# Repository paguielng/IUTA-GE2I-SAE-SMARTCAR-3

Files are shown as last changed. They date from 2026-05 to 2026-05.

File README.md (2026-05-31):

# ST STM32: development platform for [PlatformIO](https://platformio.org)








PlatformIO IDE (https://platformio.org?utm_source=github&utm_medium=core)
    
1 Présentation du projet
   ---
1.1 Contexte
   ---
Une entreprise de jouet souhaite développer une voiture pilotée par smartphone, qui intègre plusieurs fonctionnalités comme l'anticollision, le signalement d'obstacle ……

1.2 Objectifs
---
Concevoir, vérifier et valider l'électronique et la programmation d'une voiture pilotée par smartphone afin de :
- Permettre le pilotage de la voiture à partir d'un joystick virtuel sur un smartphone
- Donner, à ce véhicule, de l’autonomie dans certaines prises de décision (anticollision)
- Fournir des informations visuelles et sonores au pilote

1.3 Description de l’existant
---
La voiture est une voiture Radio Commandée déjà existante au catalogue de l'entreprise. Toute l'électronique existante a été supprimée, tout le reste est conservé (carcasse, roues, moteurs, phares …). Les éléments suivants ont été ajoutés à l'intérieur :
- Un module pont en H de référence LF298 pour alimenter le moteur de direction et le moteur de propulsion dans les 2 sens de marche
- Un buzzer passif pour générer un signal avertisseur d'obstacle ou le klaxon
- Deux capteurs infrarouges Sharp de détection d'obstacle
- 6 accumulateurs AA NiMh de 1.2V et 2300mAh en série ou 1 pack batterie de 2 accumulateurs 18650 Li ion de 3.7V de 2600mAh.

1.4 Critères d’acceptabilité du projet
---
Le chef d'entreprise souhaite qu'à la fin de l'étude, lui soient fournis :
- Un dossier de fabrication de la carte électronique (cahier de fabrication + fichiers GERBER + fichier PROTEUS)
- Un dossier technique (cahier de laboratoire + documentation technique + simulations + schémas électriques, schéma d’implantation…)
- Une démonstration avec un prototype opérationnel
- Une étude de coût unitaire pour une production de 100 exemplaires
- Une étude d'autonomie voiture à l’arrêt

2 Expression des besoins
---
2.1 Besoins fonctionnel
---
- Un prototype
- Un dossier technique (cahier de laboratoire)
- Un dossier technique de fabrication (cahier de fabrication ……)
- Une démonstration du système opérationnel

2.2 Fonctionnement global attendu
---
- La voiture est pilotée par smartphone via liaison Bluetooth grâce à un joystick virtuel
- Des dispositifs de sécurité sont mis en œuvre sur la voiture tels que des capteurs de distance d’obstacle avant et arrière, et un avertisseur sonore en fonction de la proximité de l’obstacle.
- L'avertisseur sonore peut être activé directement comme klaxon grâce à un bouton poussoir virtuel sur le smart-phone. Il est aussi possible de générer une mélodie ou des fréquences fixes.
- Un bargraphe virtuel, sur le téléphone, permet d'informer visuellement l'utilisateur de la proximité de l'obstacle à l'avant et/ou du niveau de batterie. (Le niveau de batterie sera indiqué en permanence sauf si proximité d’obs-tacle à l’avant)
- Détection (Près, Moyen et Loin) respectivement moins de 40cm, entre 40 et 60cm et au-delà
- L’utilisateur peut choisir d’activer, de façon permanente, les phares avant et arrière de la voiture grâce à un switch virtuel sur l’écran du smartphone et au besoin de passer dans un mode de gestion automatique grâce à un capteur de luminosité.
- Les phares arrière s’allument plus fort en cas de freinage.
- La température extérieure est reportée sur le smartphone.

2.3 Fonctionnement détaillé attendu
---
- Deux détecteurs de distance infrarouge (un à l’arrière et l’autre à l’avant) permettent de mesurer la distance à l’obstacle et la vitesse d'approche du véhicule, et d’identifier la zone de proximité
- Un buzzer permet d’émettre des bips plus ou moins rapprochés en fonction de la distance à l’obstacle (2 bips par seconde dans la zone Moyen et 4 bips par seconde dans la zone près). Le klaxon est prioritaire sur les bips.
- Le véhicule réduit automatiquement de 50% la consigne de vitesse dans la zone moyenne lorsque le déplace-ment s’effectue vers l’obstacle.
- Le véhicule freine à fond (inversion de la propulsion à consigne maximale), jusqu’à arrêt du véhicule, lorsque le véhicule s’approche de l’obstacle dans la zone près, et cela quel que soit la consigne.
- Les phares arrière s’allument plus fort à chaque freinage.
- Les phares avant et arrière s’allument de façon permanente si le switch virtuel est dans la position “ON” et automatiquement en cas de faible luminosité si le switch est en position “AUTO”
- ,,,,,,,,,,,

3 Contraintes
---
3.1 Coûts
---
Aucune contrainte de coût n’est imposée. En revanche un calcul de coût unitaire pour une production de 100 cartes est attendu (composants électroniques + circuit imprimé + voiture + accessoires + main d'œuvre).

3.2 Autonomie de fonctionnement
---
La voiture doit avoir une autonomie d'au moins 30 minutes avec une batterie de 6 accumulateurs NiMh de capacité 2300mAh.

3.3 Délais de réalisation
---
2h C / 28h TD / 27h TP / 25h autonomie

4 Déroulement du projet
4.1 Séquencement
   ---
- Partie électronique du projet
- Partie Numérique du projet
- Dossier de conception (cahier de laboratoire + documentation technique + simulations)
- Dossier de fabrication (cahier de fabrication + fichiers GERBER + fichier PROTEUS)

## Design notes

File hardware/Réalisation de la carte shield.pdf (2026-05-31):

# Réalisation de la carte SHIELD smartcar

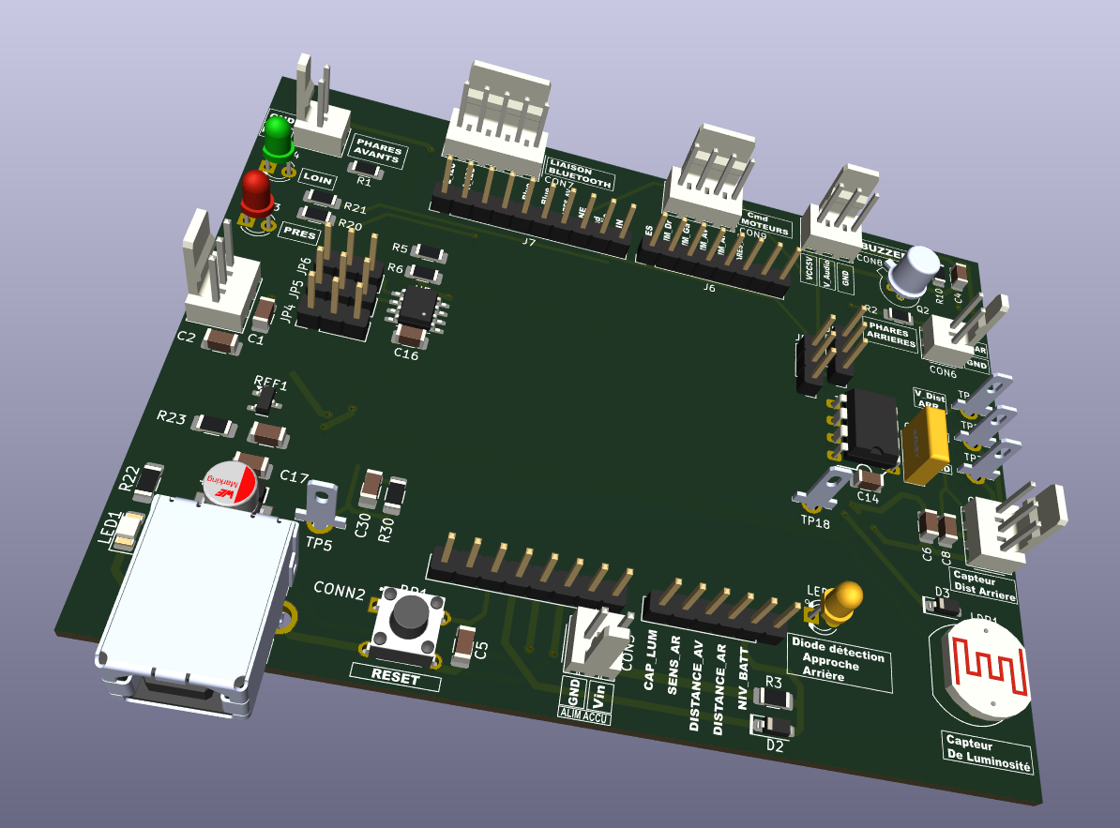
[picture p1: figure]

## I. Introduction

Le circuit imprimé est déjà commencé. Le projet KiCad se trouve dans le dossier Réalisation du circuit imprimé (https://toulouse3.sharepoint.com/:f:/r/sites/IUTA-BUTS2SAESMARTCAR_MDL/Documents%20partages/General/Partie%20Electronique/R%C3%A9alisation%20du%20circuit%20im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)

Vous devez au préalable regarder les vidéos suivantes : Alimentation en chaine (https://toulouse3.sharepoint.com/:f:/s/IUTA-BUTS2SAESMARTCAR_MDL/EhpyGaySZhJNksRkxSJ0DuYBxVbpqpTwTZGnaVfsGNpclQ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)

## II. Placement des composants

### 1) Listes des composants à placer, grille et pas de grille

- Zoom
La façon la plus simple de zoomer est d'utiliser la molette de la souris.
- La grille (voir page 27 du tutoriel)
La grille permet d'aligner tous les objets (composant, pistes, ..). Vous devrez toujours travailler en millième de pouce (mils) avec un pas de grille de 10millièmes de pouce 10 mils sauf lors de placement nécessitant une grande précision 2mils.
- Placer un composant (A partir de la page 29 du tutoriel)
- Rotation des composants ou sérigraphie grâce à la touche R après une sélection -
- Sélection d’une piste entière grâce à la touche U lors d’un survole de la souris
- Pour déplacer un composant déjà placer : clic droit pour le sélectionner puis maintient clic gauche pour le déplacer.

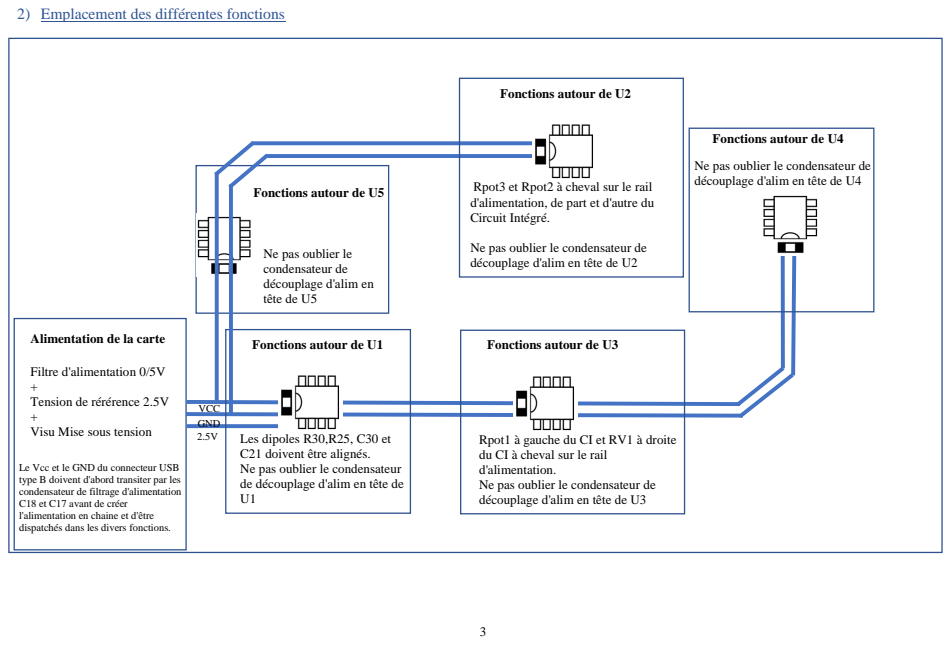
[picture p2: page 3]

2) Emplacement des différentes fonctions

Ne pas oublier le condensateur de
découplage d'alim en tête de U4

Rpot3 et Rpot2 à cheval sur le rail
d'alimentation, de part et d'autre du
Circuit Intégré.

Ne pas oublier le
condensateur de
découplage d'alim en
tête de U5

découplage d'alim en tête de U2

Les dipoles R30,R25, C30 et
C21 doivent être alignés.
Ne pas oublier le condensateur
de découplage d'alim en tête de

Rpot1 à gauche du CI et RV1 à droite
du CI à cheval sur le rail
d'alimentation.
découplage d'alim en tête de U3

Le Vcc et le GND du connecteur USB
type B doivent d'abord transiter par les
condensateur de filtrage d'alimentation
C18 et C17 avant de créer
l'alimentation en chaine et d'être
dispatchés dans les divers fonctions.

### 3) Placement de l'ensemble des composants

Avec la grille en système impérial, une grille de 10mils ou 2th.
- Placer U11 et les composants associés aux fonctions autour de ce Circuit Intégré (voir les directives de la page précédente).
- Placer U3 et les composants associés aux fonctions autour de ce Circuit Intégré (voir les directives de la page précédente).
- Placer U5 et les composants associés aux fonctions autour de ce Circuit Intégré (voir les directives de la page précédente).
- Placer U2 et les composants associés aux fonctions autour de ce Circuit Intégré (voir les directives de la page précédente).

## III. Routage

### 1) Les règles de conception

Les pistes possèdent des largeurs spécifiques suivants leur nature.
Les pistes d'alimentation repérées 5V et GND auront une taille automatique de 30mils et les vias associés seront des V70mils.
Les pistes de signal (toutes les autres pistes) auront une taille automatique de 20mils et les vias associés seront des V50mils.

Les règles d'isolement sont définies dans les options.
C’est-à-dire les distances minimums entre chaque entité.
- 10mils pour les distances minimum entre toutes les entités).
- Pad-Pad (distance minimale entre deux Pastilles) 10mils
- Pad-Trace (distance minimale entre une pastille et une piste) 10mils
- Trc-Trc (distance minimale entre deux pistes) 10mils
- Graphic (distance minimale entre deux graphiques) 10mils
- Edge (distance minimale avec le bord de la carte) 10mils

Rappel : 1mil est 1 millième de pouce
1 pouce est égal à 2.54cm soit 25.4mm
D'où 1mil = 0.0254mm

### 2) L'empilement des couches

Nous travaillerons sur une carte électronique double face, c’est-à-dire 2 couches de cuivre :
- Une couche de cuivre (de couleur rouge dans KiCad) sur le dessus de la carte ( Cette face se nomme côté composants car c'est sur cette face que nous trouvons, généralement, les composants électronique)
- Une couche de cuivre (de couleur bleu dans KiCad) sur le dessous de la carte (Cette face se nomme côté cuivre car c'est historiquement la face cuivrée des premiers Circuits Imprimés)

Nous utiliserons une épaisseur standard de cuivre de 35µm (Top copper et Bottom copper) sur une carte d'épaisseur finale 1,6mm. Le matériau central est de type FR4. Une couche de verni de 10µm (Top resist et

Les 2 couches de verni de 10µm | Les 2 couches de cuivre de 35 µm

La déclaration des couches se fait dans le menu « Options »

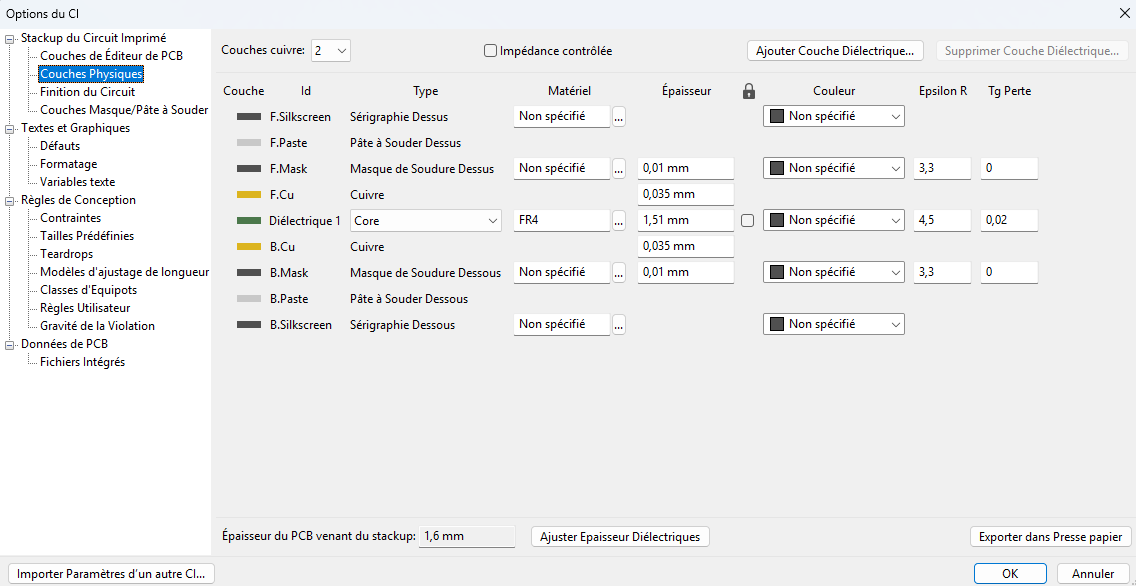
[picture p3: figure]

### 3) Les pistes

Remarques générales :
- Les pistes ne doivent pas faire de boucle sinon il risque d'y avoir du bruit électrique (parasites).
- Pas d’angle droit dans les changements de direction. Seuls les changements de direction à 45° sont autorisés.
- Pas d’angle inférieur à 90° dans les raccords de piste
- Routage automatique interdit car ne respecte pas les règles de placement et de réduction du bruit.
- Visionner les vidéos sur le routage
a) Pistes d'alimentation en chaine

Les pistes d'alimentation 5V et GND autorisant l'alimentation en 0/5V de toutes les fonctions doivent, à partir des condensateurs de filtrage d'alimentation C18 et C17, cheminer parallèlement avec un écart de 10th (2 carreaux avec une grille de 5th) sur le côté cuivre.
Les pistes d'alimentation sont déjà tirées, il manque juste à les raccorder à la sortie du filtre d'alimentation composé de C18 et C17.
Ce cheminement parallèle des pistes d'alimentation permet de limiter les parasites électromagnétiques engendrés par les fluctuations de courants sur les liens d'alimentation.

La tension de référence 2,5V fournit par REF1 doit transiter par le condensateur de découplage C19 avant d’être raccordée à U1

Voir page 3 pour la vue d'ensemble et les directives supplémentaires.

En vous aidant du tutoriel KiCad tracer les 3 arrivées GND, VCC et 2,5V et raccordez les au rail d'alimentation déjà tiré.

L'alimentation des différentes fonctions se fait en repiquant les 2 liens d'alimentation en un seul endroit du cheminement de l'alimentation en chaine.

Router l'ensemble des composants de la fonction "Alimentation".

b) Condensateur de découplage d'alimentation
Les condensateurs de découplage d'alimentation sont présents pour filtrer les fluctuations de tension sur les pistes d'alimentation.
Les pistes d'alimentation, des fonctions concernées par ces condensateurs, doivent tout d'abord transiter par ces condensateurs avant d'alimenter la fonction.

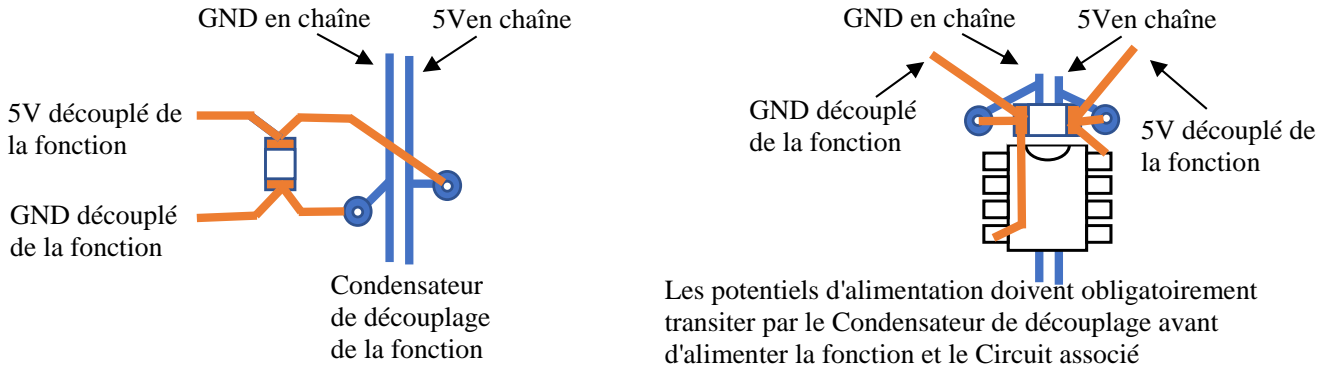
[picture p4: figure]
Condensateur de découplage de la fonction; 5V découplé de la fonction; GND découplé de la fonction; GND en chaîne; 5Ven chaîne; GND découplé; de la fonction; 5V découplé de; la fonction; Les potentiels d'alimentation doivent obligatoirement

c) Les composants d'une fonctions
Tous les composants de chaque fonction se situent dans la même zone de la carte de façon à minimiser les longueurs des pistes. Si ce n'est pas le cas retoucher votre placement.

Router l'ensemble des composants fonction par fonction.

d) Alimentation locale des fonctions
L'alimentation de chaque fonction devra s'effectuer exclusivement via le condensateur de découplage si celui-ci existe.
Alimentation locale d'une fonction => L'alimentation de chaque fonction ne peut se faire qu'en un seul point ou zone sur l'alimentation en chaine. Interdiction de se repiquer à plusieurs endroits (ne pas suivre le chevelu

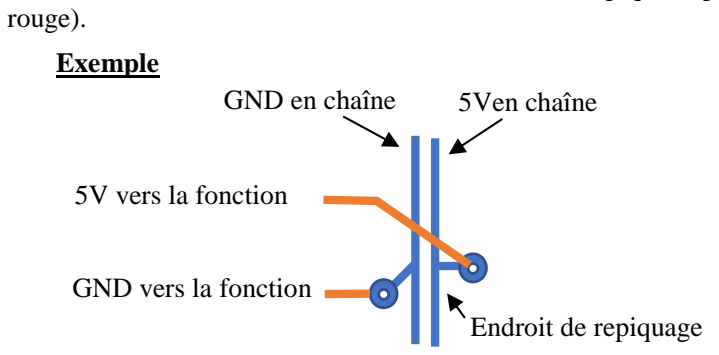
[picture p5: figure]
rouge).; GND en chaîne; 5Ven chaîne; GND vers la fonction; 5V vers la fonction; Endroit de repiquage; Exemple

e) Vérification d'absence d'erreur DRC
Vous devez avoir ces informations en bas à droite de la fenêtre : | et
Si non, vous devez corriger les erreurs.
Les erreurs DRC sont les erreurs où vous ne respectez les distances d'isolements et les erreurs CRC sont des oublis de pistes.

## IV. Sérigraphie

La sérigraphie constitue l'ensemble des écritures, indications et dessins qui seront sérigraphiés sur le verni de la carte.
Nous écrirons uniquement sur le côté composant. Ce qui correspond à la couche | mais nous
aurions pu écrire sous la carte (coté cuivre) ce qui correspond à la couche | . Sur le côté
cuivre les écritures et dessins apparaissent Rose et les écritures sont en mirroir.

transiter par le Condensateur de découplage avant d'alimenter la fonction et le Circuit associé

### 1) Le nom des composants

Tous les composants sont repérés par un nom. Par exemple :
- les résistances sont repérées par le suffixe R suivi d'un nombre
- les condensateurs sont repérés par le suffixe C suivi d'un nombre
- …

Cela permet non seulement de repérer l'emplacement physique des composants au moment du placement mais aussi de repérer les points de mesures pour des tests ou dépannages futurs.

La sérigraphie ne peut se faire sur les zones exemptent de vernis comme les pastilles. En effet les pastilles des empreintes des composants ne sont pas recouvertes de vernis de façon à permettre la soudure.

En vous plaçant sur une petite grille, 5th par exemple, affiner la position du nom des composants de façon à pouvoir lire les écritures même si les composants sont en place.

Pour modifier l'angle d'écriture sans modifier la position de l'ensemble du composant :
Clic droit sur le nom du composant pour le sélectionner puis clic gauche pour le sélectionner + R

Quelques exigences :
- Le nom du composant doit pouvoir être lu après la soudure de celui-ci => Pas de nom sous le composant.
- Les noms des composants proches devront, si possible, être alignés verticalement ou horizontalement
- Les noms des composants peuvent être au besoin tournés de 90° dans le sens trigonométrique
- L'ensemble des écritures et dessins doit apparaitre en jaune pâle
- Aucun dessins ou écritures ne doit apparaitre en rose (écriture en dessous)

### 2) Noms du binôme et personnalisation

Placer vos noms et groupe sur la carte avec une police de caractères "Arial Black" et une hauteur de 0,1inch.

Customiser votre carte en ajoutant une image ou photo monochrome.

## V. Création des fichiers de fabrication

Utiliser le tutoriel KiCad

Le fichier gerber ZIP est l'élément essentiel du dossier de fabrication.

## VI. Règles de notation appliquées colonne D du fichier de validation

- L'alimentation doit être en chaine ne doit pas comporter de boucle (-0.5 si non respecté)
- Les condensateurs de découplage doivent être très proche du circuit intégré (s'il y en a un) et respecter les règles de routage (voir III.3)b)) (1 point si correcte, 0.5 point si 1 erreur, 0 point sinon)
- Les composants doivent être regroupés par fonction (1 point si correcte, 0.5 point si 1 erreur, 0 point sinon)
- Les GND et VCC de chaque fonction doivent être pris localement sur le condensateur de découplage d'alimentation (1 point si correcte, 0.5 point si 1 erreur, 0 point sinon)
- Les noms du binôme et le groupe doivent être présent (0.5 point)
- Les noms des composants sont lisibles après soudure des composants (0.5 point)
- Les pistes autorisées sont horizontal, vertical et à ±45° (si non -0.5point)
- S'il existe des pistes manquantes (-1 point)

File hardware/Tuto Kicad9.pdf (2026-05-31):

1 | CDS

Christophe DOS SANTOS

# KiCad 9

## Table des matières

e) Transfert d’un ou plusieurs composant(s) d’une librairie à une autre ( méthode 2) 18 c) Placer précisément un composant avec l’outil de positionnement interactif ....31

## I. Saisie de schéma

1) Généralités
2) Importer un schéma électrique non KiCad

Numérotation automatique dans l’ordre de dépôt

Fils uniquement horizontaux et verticaux

Grille nécessaire pour un alignement des composants.

Possibilité de numérotation automatique des composants, à postériori.

3) Feuille de travail et cartouche
4) Dépôt du symbole d’un composants, en librairie, sur le schéma
Click | Indiquer le nom du composant à placer
| Sélectionner la version du composant

Sélectionner
l’empreinte du
composant

Cliquer ici si dépôt de
plusieurs instances

Click

Taille de la
feuille

Renseignements

5) Propriétés des composants
Pour éditer les propriétés d’un composant
6) Grille
Changement de grille par clic droit sur la feuille

La gestion de la grille par type d’objet se fait à partir du menu « préférences » puis « Préférences »

Click droit

Référence du composant
Valeur du composant

Ajouter une
propriété
comme la
référence
vendeur

7) Arrivées des potentiels d’alimentation (POWER)
Sous kicad il est nécessaire d’ajouter un POWER FLAG pour identifier les sources d’alimentation. Sans POWER FLAG vous obtiendrez des warnings au moment de la vérification des règles électriques.
8) Contrôle des règles électriques

Exemple de POWER FLAG

Le POWER FLAG
est accessible
dans la librairie
« Power »

9) Assigner les empreintes aux composants du schéma

Remarque : Certaines empreintes notamment celles des résistances CMS sont légèrement plus grande pour la soudure à la main. Elles sont annotées « Hand_Solder »

Click

Filtrer par librairie

1) Sélectionner le composant
2) Sélectionner la librairie
4) Sélectionner l’empreinte
3) Afficher l’empreinte
5)Afficher la vue 3D de l’empreinte | 6) Sauvegarder les modifications

Click droit sur un
composant de la liste
pour faire apparaitre un
menu contextuel

Copier l’empreinte du
composant sélectionné

Coller l’empreinte
précédemment copiée

## II. Symboles électriques et librairies

1) Créer un symbole
a) Lancer l’éditeur de symbole
b) Créer un symbole à partir d’un composant existant

Clic sur l’éditeur de symbole pour lancer la fenêtre dédiée

Chercher un
composant qui
se rapproche le
plus du
composant à
dessiner

Ajouter des entrées ou des sorties. Modifier le corps du symbole, les noms des E/S, les numéros de broche, le texte ….

Dans le menu fichier | Donner un nom au composant

Sélectionner une librairie personnelle si elle existe

Créer une nouvelle librairie si vous ne possédez pas de librairie personnelle ou souhaitez créer une autre librairie.

c) Créer un symbole de A à Z

Clic sur l’éditeur de symbole pour lancer la fenêtre dédiée

Choisir la librairie de
destination puis
cliquer sur nouveau
composant

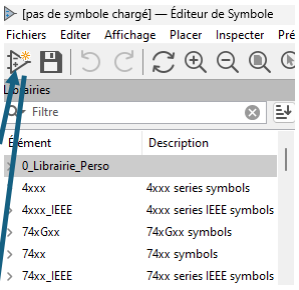
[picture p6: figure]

Nom du nouveau composant

Si le composant existe déjà dans une autre librairie

Préfixe du composant (exemple R pour resistor)

Nombre de composants identiques dans le même boitier

Clic gauche sur le corps pour accéder aux propriétés

Dessiner le composant

Choisir » remplir avec » pour donner une couleur au fond

Dessiner le corps du composant avec des formes prédéfinies, des arcs, des segments …..

Clic gauche pour commencer, clic gauche pour les changements de direction puis double clic gauche pour finir.

Dessiner le composant (suite)

Dessiner les broches
Placer du texte
Placer du texte dans une
boite

Accéder aux propriétés du symbole

Visibilité et apparence du nom et de la valeur
Localisation de l’empreinte dans les librairies d’empreinte.
URL de la documentation

Description du composant : Fonction, empreinte, ….

Choisir la couleur du corps désirée, ici jaune pâle.

Placer des mots clés comme par exemple : résistance, AOP, régulateur…

Donner un nom

2) Listes des sites permettant de télécharger des symboles
- Outils du revendeur Mouser : https://www.mouser.fr/electronic-cad-symbols-models/
- SnapEda : https://www.snapeda.com/
- SamacSys : https://www.samacsys.com/
- Les sites de revendeur comme Farnell et Radiospares

Sauvegarder le
composant

Clic

référence revendeur, le prix, ….

3) Les librairies de symboles
a) Emplacement des librairies et généralités Les librairies de base de Kicad se situent par défaut :

Les librairies personnelles ou propre au projet se situent par defaut :

Ne pas utiliser ou créer des librairies dans « Documents » si vous souhaitez une portabilité du projet.

(Voir f) Portabilité des librairies)

Pour configurer les librairies :

Examinateur de librairies de composants.
Permet de visionner les symboles des librairies mais pas de configurer les librairies.

Click

Ensemble des
librairies globales

de composants
disponibles

Possibilités d’ajouter
ou de supprimer des
librairies

Librairies utilisées pour la portabilité du projet

(Voir f) Portabilité des
librairies)

b) Création d’une librairie par importation d’un symbole de composant
Après téléchargement des fichiers, le fichier correspondant au symbole se termine avec l’extension .kicad_sym ou .lib.

Clic

1)Clic pour
ajouter la
librairie qui
contient le
nouveau
symbole

2)Une nouvelle ligne
apparaît | 4)Clic sur le dossier pour
| rechercher le fichier librairie
| de symboles

5)Sélectionner le fichier désiré

Clic

3)Donner un nom évocateur à cette librairie

Le fichier est en .sym pour symbol

Librairies utilisées pour la portabilité du projet
(Voir f) Portabilité des
librairies)

c) Ajout d’un composant dans une librairie existante
d) Transfert d’un composant d’une librairie à une autre (méthode 1)

1)Clic sur éditeur de symbole

Dans le fichier schématique

Ou

Dans le fichier projet

2)Clic droit sur la
librairie de
destination

3)Choisir le
symbole à
importer

2)Sélectionner
une librairie

1)Clic sur éditeur de symbole

Dans le fichier schématique

Ou

Dans le fichier projet

Sélectionner la librairie de destination -> clic droit -> coller

e) Transfert d’un ou plusieurs composant(s) d’une librairie à une autre ( méthode 2) Ouvrir le fichier de la librairie, où se situe le composant, avec un éditeur de texte.

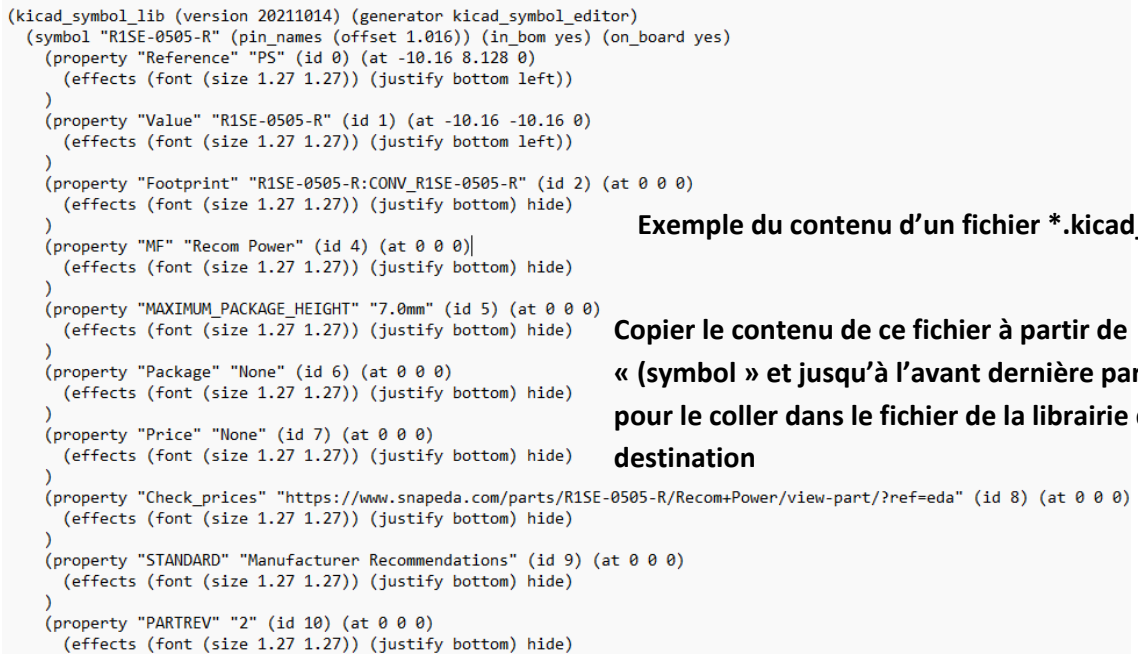
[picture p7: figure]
destination

Ouvrir le fichier de la librairie de destination dans l’éditeur de texte et se placer juste avant la dernière parenthèse et coller le contenu du fichier précédent.

Puis enregistrer ce fichier

Exemple du contenu d’un fichier *.kicad_sym

Copier le contenu de ce fichier à partir de
« (symbol » et jusqu’à l’avant dernière parenthèse pour le coller dans le fichier de la librairie de

3)Sélectionner le ou les
composants à transférer
puis clic droit

Copier ou Couper suivant
que vous souhaitez laisser une copie.

Remarque : L’ancienne librairie peut être supprimée.

f) Portabilité des librairies Voir : page 64
4) Liste du matériel BOM (Bill Of Material)

Sélectionner la librairie
à supprimer puis poubelle

Dans le menu « outils »

Sélectionner les champs
intéressant. Ici référence, valeur, quantité et
regroupement par valeur

Choisir le
format de
sortie CSV
pour l’ouvrir
avec excel ou
autre

Création
du fichier

## III. Création du PCB

1) Contrôle des règles électriques du schéma
2) Lancer l’éditeur de PCB

Clic sur l’éditeur de PCB pour lancer la fenêtre dédiée

L’ensemble des
composants à placer est
regroupé au milieu.

ClickC

Click

Toutes les erreurs ou avertissements signalés ici sont indiquées sur le PCB par une flèche de couleur.

Clic droit sur l’erreur ou l’avertissement pour être placé à l’endroit exact du PCB.

Nécessaire pour détecter d’éventuelles erreurs électriques

Toutes les règles de
violation sont
accessibles ici

3) Définition des Propriétés du projet
a) Les couches graphiques

Dans le menu « fichier » choisir Options « CI »

OU

Directement par l’icone

Pochoir pour le dépôt de pâte à braser sur le dessus Sérigraphie sur le dessus
Emplacement du vernis sur la couche du dessus Emplacement du Cuivre sur la couche du dessus

Sérigraphie sur le dessous

Bord de la carte

Emplacement du Cuivre sur la couche du dessous Emplacement du vernis sur la couche du dessous

Pochoir pour le dépôt de pâte à braser sur le dessous

b) Les couches physiques (Données fournies sur le site du fabricant)
c) Finition du cuivre (Voir possibilités du fabriquant)
d) Définitions des frontières Vernis/Masque/cuivre

e) Propriétés du texte et graphiques en fonction des couches
f) Contraintes d’isolement/de perçage g) Classes d’équipotentielles
Afin de gérer automatiquement les largeurs de pistes il est intéressant d’assigner des largeurs de piste aux équipotentielles de la carte.
Nous allons définir 3 classes :
- VBATT : Alimentation commune de la carte et des moteurs à partir des batteries ; largeur de piste 30th soit 0.762mm et via de 70th soit 1.78mm
- POWER : Alimentation 5V et GND de la partie commande de la carte ; largeur de piste de 20th soit 0.508mm et via de 50th soit 1.27mm
- DEFAULT : Tous les autres potentiels ; largeur de piste de 15th soit 0.38mm et via de

Une fois défini les classes d’équipotentielles il faut les assigner sur la schématique.

Remarques :

- Faire de même pour tous les fils en lien avec les équipotentielles autres que défaut.
- Ne pas oublier de mettre à jour le PCB à partir du schéma.
h) Taille des pistes et vias prédéfinie

70 mils35 mils70 mils

Clic droit sur le fil pour faire apparaitre le menu contextuel du fil.

Clic

Choisir la classe
d’équipotentielle,
précédemment crée,
correspondant aux pistes
d’alimentation 5V. (ici
« power »)

Clic

Clic
OU

Clic

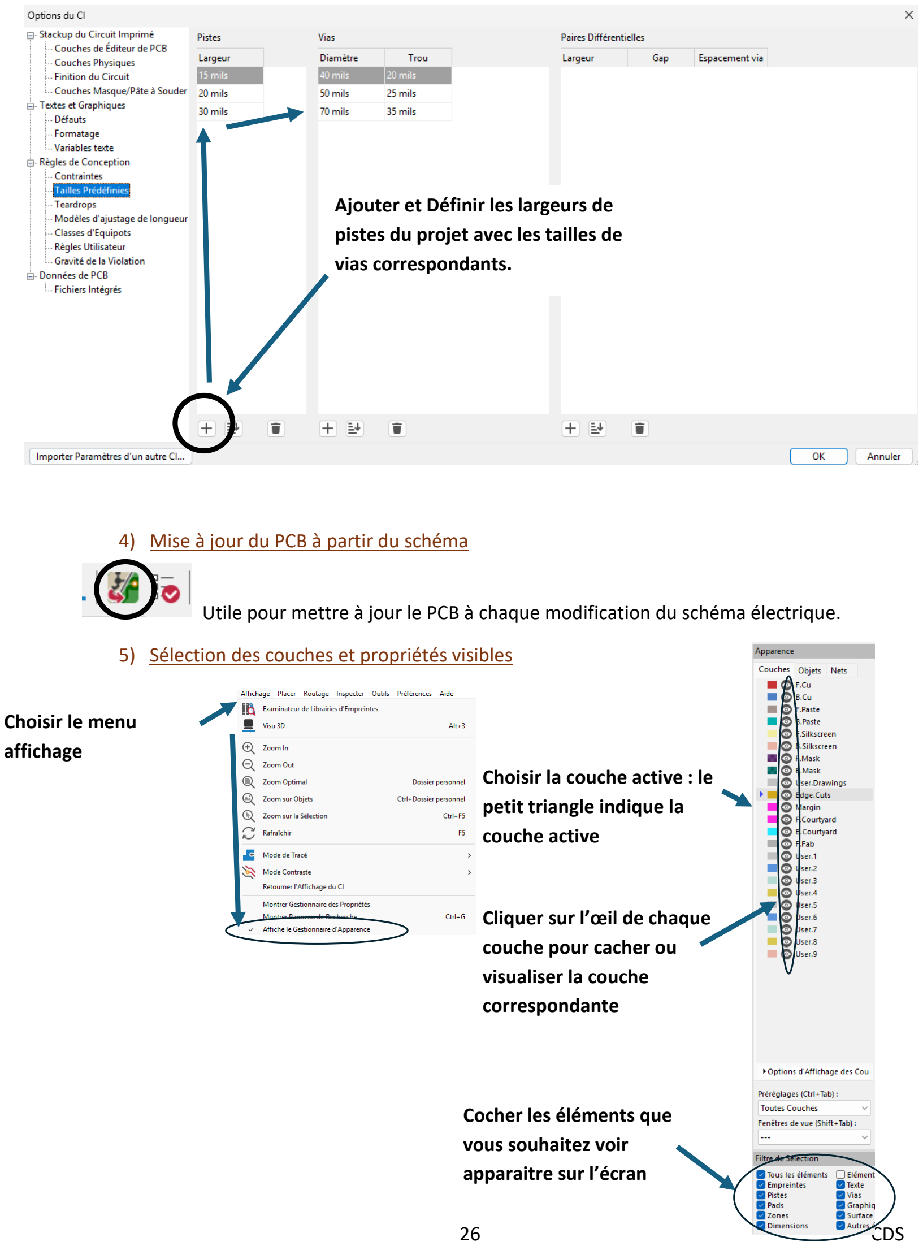
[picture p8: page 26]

4) Mise à jour du PCB à partir du schéma

Utile pour mettre à jour le PCB à chaque modification du schéma électrique.

5) Sélection des couches et propriétés visibles

Choisir le menu
affichage
Choisir la couche active : le petit triangle indique la
couche active

Cliquer sur l’œil de chaque couche pour cacher ou
visualiser la couche
correspondante

Cocher les éléments que
vous souhaitez voir
apparaitre sur l’écran

Ajouter et Définir les largeurs de pistes du projet avec les tailles de vias correspondants.

6) Choix du pas de grille et de la couche de travail
7) Tracer des contours et des trous de fixation de la carte
a) Choisir la couleur des bords de la carte
Choix du pas de grille | Choix de la couche de
| travail

Afficher la grille
Activer la grille
Choisir l’unité d’affichage des longueurs

b) Choix de la couche et de la grille

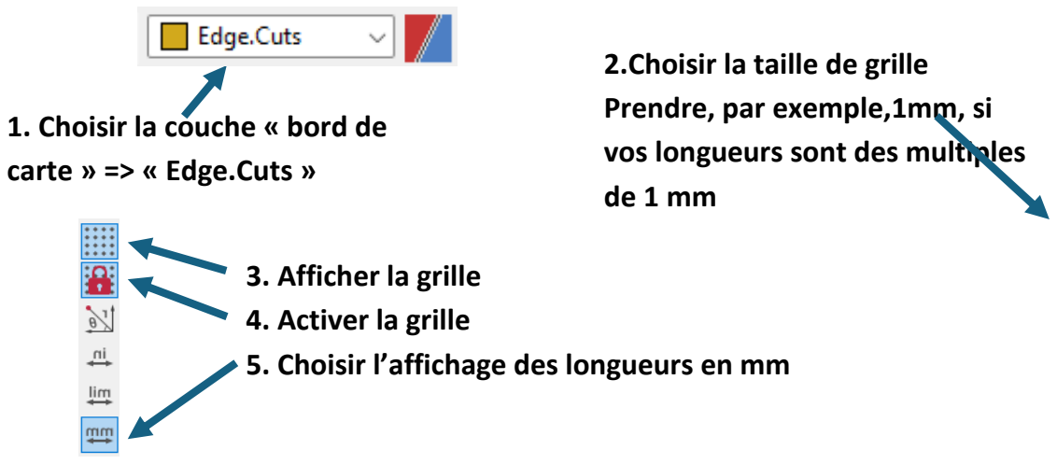
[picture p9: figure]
1. Choisir la couche « bord de carte » => « Edge.Cuts »; 2.Choisir la taille de grille Prendre, par exemple,1mm, si vos longueurs sont des multiples de 1 mm; 3. Afficher la grille 4. Activer la grille

c) Tracer du contour de la carte
d) Tracer les trous de fixation

### 5. Choisir l’affichage des longueurs en mm

Un clic gauche pour initier le tracé et un deuxième clic gauche pour finir le tracé

Les dimensions de la forme sont indiquées au cours du tracé

Choisir la couche « bord de carte » => « Edge.Cuts »

1.Choisir l’outil
Tracer Cercles

2.Clic gauche au centre du cercle puis deuxième clic
gauche lorsque le rayon
désiré est atteint.

8) Placement des composants
a) Tracer des cotes pour l’aide au placement
Se placer avec un affichage des longueurs en mm

A l’aide de l’outil de cotation tracer toutes les cotes.

Un gauche clic pour débuter la cote et un deuxième clic gauche
pour terminer la cote, puis un troisième clic gauche pour la positionner

Remarque : Pour cette phase il est bien de rester sur une grille en mm.

b) Placer les composants
Tous les composants à placer sont regroupés sur une partie de l’écran :

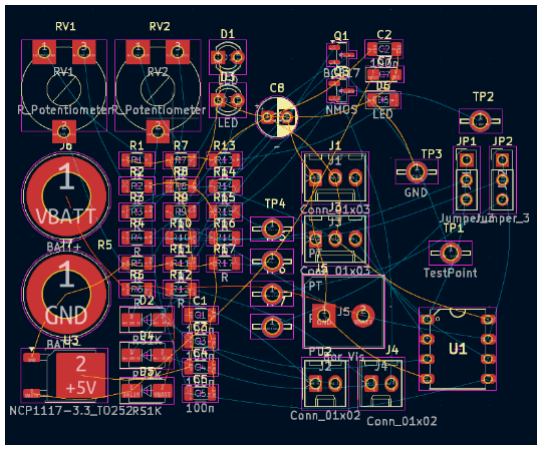
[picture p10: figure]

- Si certains composants à placer sont positionnés au mm alors se placer sur une grille en mm
sinon se placer sur une grille en th ou mils (25mils) car la plupart des empreintes ont été crées sur des grilles en mils ou th. Ceci permettra un bon alignement des pistes entre les composants.
- Choisir l’outil de sélection
- Clic gauche sur la sérigraphie du composant à placer pour le mettre en surbrillance puis maintien clic gauche pour le déplacer (ou touche M).

Raccourci

« M »

- Clic droit sur le composant pour ouvrir le menu contextuel afin de le manipuler et de

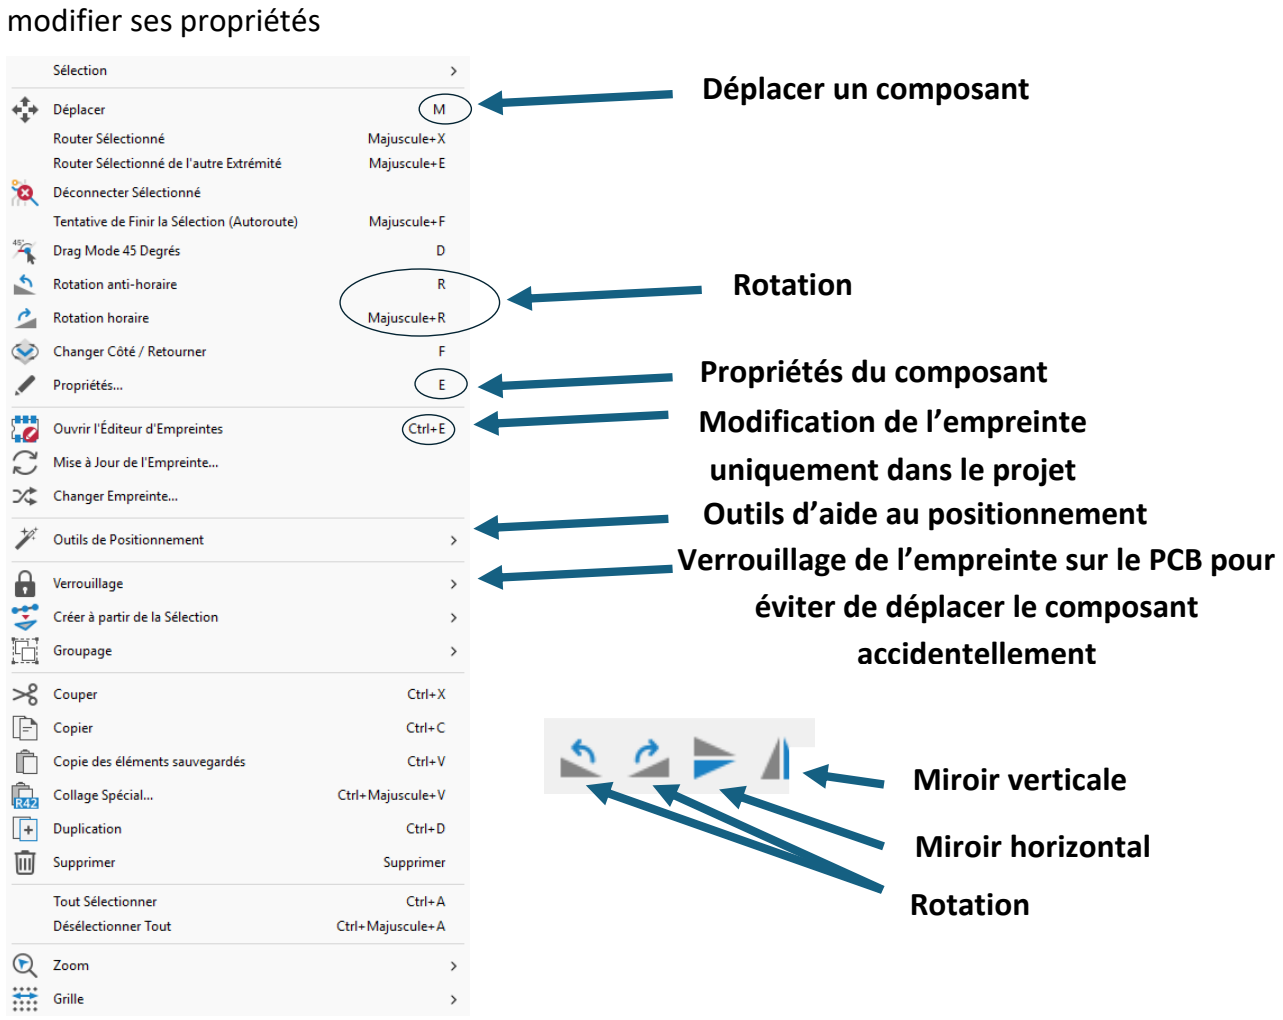
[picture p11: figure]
modifier ses propriétés; Déplacer un composant; Rotation; Propriétés du composant; Modification de l’empreinte uniquement dans le projet; éviter de déplacer le composant accidentellement; Outils d’aide au positionnement; Miroir verticale; Miroir horizontal

Verrouillage de l’empreinte sur le PCB pour c) Placer précisément un composant avec l’outil de positionnement interactif 1.Clic droit sur le
composant à placer pour
le sélectionner

2.Clic

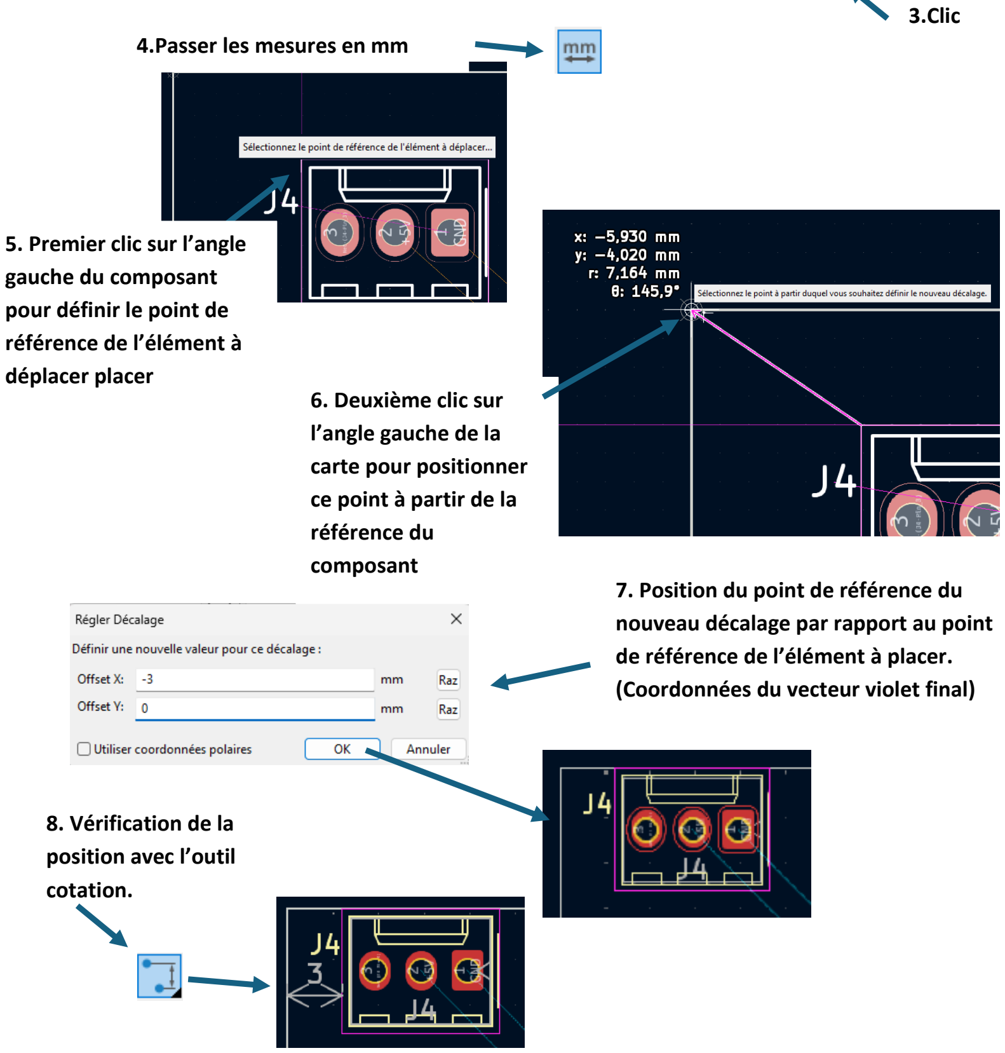
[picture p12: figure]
3.Clic; 4.Passer les mesures en mm; 5. Premier clic sur l’angle gauche du composant pour définir le point de référence de l’élément à déplacer placer; 6. Deuxième clic sur l’angle gauche de la carte pour positionner ce point à partir de la référence du composant; 7. Position du point de référence du nouveau décalage par rapport au point de référence de l’élément à placer. (Coordonnées du vecteur violet final); 8. Vérification de la position avec l’outil cotation.

d) Déplacer un composant avec les pistes
9) Tracer une piste
a) Taille de la piste
b) Couche de la piste
c) Pas de la grille

Choisir l’outil
Tracer de piste

Choisir une taille de
piste prédéfinie

Choisir une taille de piste automatique (voir Classes
d’équipotentielles)

Choisir la couche
concernée

Choisir le pas de la
grille

OU Touche « + » ou « - «

4.Touche « B » pour prendre en compte les

d) Tracé de la piste
e) Changement de couche par la création d’un via
10) Modification d’une piste
a) Sélectionner la piste
- Clic gauche sur la piste pour sélectionner un segment
- Survoler la piste + U : permet de sélectionner une piste entre 2 pastille ou embranchement.
- CTRL + clic gauche pour sélectionner plusieurs segments
b) Changer la taille d’une piste
Clic droit sur la piste sélectionnée pour faire apparaitre le menu contextuel.

Clic gauche sur la
pastille de départ

Clic gauche sur la
pastille de d’arrivée

Clic gauche à chaque changement de direction si nécessaire

Clic sur propriétés

Changer la taille de la piste.
Se placer au préalable en mm ou en mils pour obtenir les mesures dans l’unité souhaitée.

Clic droit sur la piste à l’endroit du via
OU
Touche de raccourci : V + clic gauche

c) Suppression des pistes
Suppression des pistes sélectionnées : touche « Suppr »
11) Tracer la sérigraphie d’une empreinte

Exemple de tracé

Choisir l’outil de tracé

La couche
sérigraphie du
dessus doit être

Tracé d’un trait de 4.95mm de hauteur

Choisir l’outil de duplication pour dupliquer la ligne de 5mm (préférer le raccourci « Ctrl + D »

Choisir l’outil de rotation pour tourner de 90° la ligne dupliquée (préférer le raccourci « R »)

Nous n’avons pas tracé un carré pour pouvoir opérer la modification ci dessous

Se placer dans l’éditeur d’empreinte

12) Modifier les propriétés de la pastille par défaut

Raccourcir les 2 côtés de l’angle en haut à gauche.

Ajouter un segment pour indiquer le sens du composant borne

Ajouter un cercle pour indiquer la borne 1 du composant

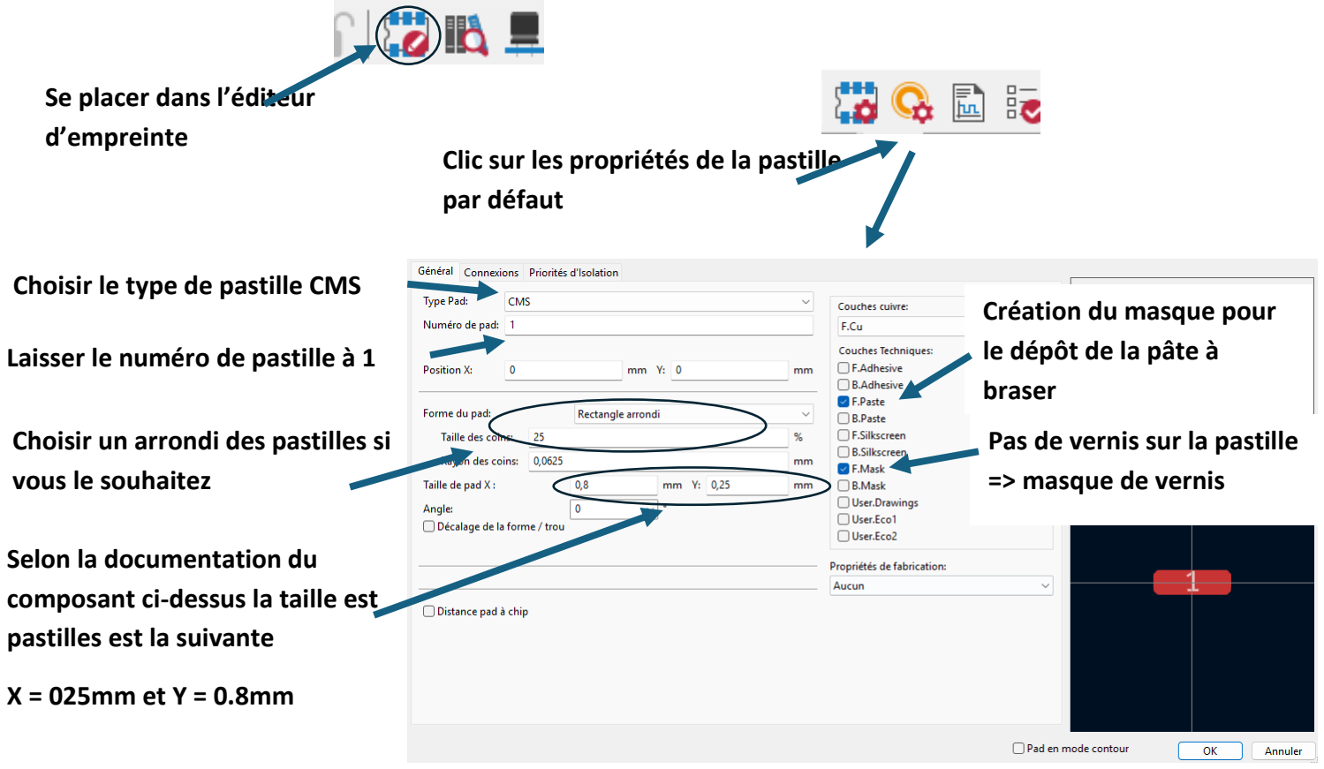
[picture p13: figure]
Clic sur les propriétés de la pastille par défaut; Choisir le type de pastille CMS; Choisir un arrondi des pastilles si vous le souhaitez; Selon la documentation du composant ci-dessus la taille est pastilles est la suivante; Laisser le numéro de pastille à 1; Pas de vernis sur la pastille => masque de vernis; Création du masque pour le dépôt de la pâte à braser; Se placer dans l’éditeur d’empreinte

13) Modification des propriétés d’une pastille

Clic droit sur la pastille pour afficher et modifier les propriétés (voir ci-dessus)

14) Dupliquer et modifier l’orientation des pastilles Exemple de création

Se placer dans l’éditeur
d’empreinte

Les pastilles commencent à 0.6 du bord et sont espacées de 0.5mm

Choisir l’outil de mesure pour repérer cette distance de 0.6mm

Avec l’outil de sélection ,la duplication « Ctrl+D », la rotation « D », la désélection « Ctrl + clic gauche » placer les 24 autres pastilles

Se placer dans l’éditeur
d’empreinte

15) Numéroter les pastilles

Un clic gauche sur chaque pastille dans l’ordre de numérotation.

16) Création de la zone d’exclusion de l’empreinte
Cette zone permet de définir l’occupation physique du composant et de prévenir tout chevauchement avec des composants voisins

Choisir la couche de travail pour délimiter la zone d’occupation de l’empreinte

Choisir une grille avec un pas de 0.05mm ce qui correspond à environ 2 millièmes de pouce

Choisir l’outil de dessin trait et tracer 4 traits à 0.25mm de l’empreinte soit environ 10 millièmes de pouce.

Clic droit sur la zone de travail pour accéder au menu contextuel

17) Création de pad thermique pour la diffusion de la chaleur Exemple de création de pad thermique

Résultat avec 25 pads thermiques

Clic

Clic droit sur la pastille pour accéder au menu contextuel et la modifier en rectangle
3.7mm*3.7mm

Numéroter la pastille 33

Choisir Pad traversant

Numéro 33

Aucune couche
technique

Choisir Pad
thermique

Diamètre de la
pastille 0.5mm

Diamètre du trou
0.2mm

18) Création des emplacements de dépôt de pâte à braser
Exemple
Définition des emplacements de dépôt de la pâte à braser qui évitent les trous des vias thermiques.
Se placer sur la couche
de la pâte à braser du
dessus

Utiliser l’outil de tracé de polygone pour tracer la zone de base qui sera dupliquée.

Dupliquer et étendre cette zone sur l’ensemble de la
pastille.

19) Vérifier la validité d’une empreinte

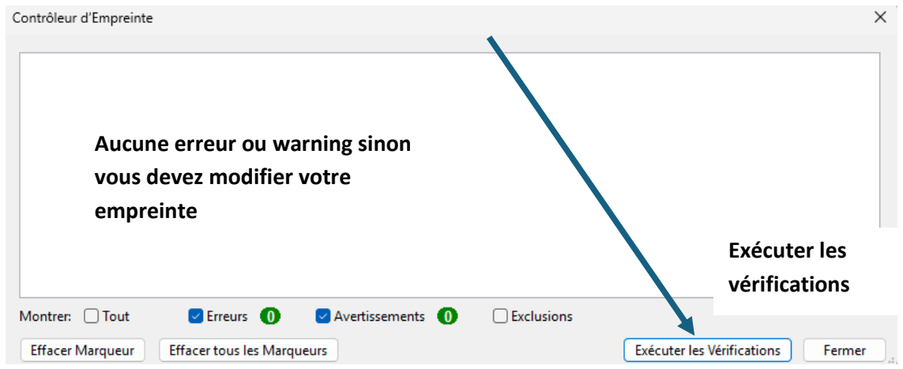
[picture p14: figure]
Exécuter les vérifications; Aucune erreur ou warning sinon vous devez modifier votre empreinte

20) Créer une empreinte
a) Lancer l’éditeur d’empreinte Clic sur l’éditeur
d’empreinte pour
lancer la fenêtre
dédiée

Lancer l’outil de contrôle d’empreinte

b) Créer une empreinte à partir d’une empreinte existante

3.Choisir d’afficher la grille

4.Verrouiller les objets sur la grille

5.Choisir une grille en mm ou mil suivant le centrage
existant des pastilles

1.Faire une recherche par mot clé

Ou

1.Aller chercher directement l’empreinte dans la librairie

2.Double cliquer sur l’empreinte pour ouvrir la fenêtre d’édition

### 6. Choisir le pas de grille qui

permet de centrer, les
pastilles existantes, sur la grille

Clic droit sur une pastille (pad) Pour le dupliquer

Ajout d’une pastille en
respectant les distances
interpastille et l’alignement | Décalage de la barre
inférieure de la
sérigraphie du boitier

Modification de
l’encombrement du
boitier du composant
(en gris)

Modification de la zone
d’exclusion des
composants voisins
(en violet)

Clic droit pour accéder au menu contextuel

Cliquer dans l’ordre croissant sur les pads pour les renuméroter

Voir page suivante pour la modification du pad 9

Clic droit sur le pad 9
puis propriétés

Choisir général

Augmenter la
taille de y de 25%
soit 0.4mm de plus

Ajout de 6 vias (pad)
thermique pour la diffusion de chaleur vers les plans de masse

Changer le nom de
l’empreinte par « clic
gauche » + « propriétés »

Modification des propriétés de l’empreinte :

Sauvegarder l’empreinte dans une librairie personnel

Dans le menu fichier :
« Sauvegarder Sous »

2.Sélectionner la librairie d’empreinte de destination ou en créer une

1.Donner un nom à
l’empreinte

3.Clic

Nom de l’empreinte dans la librairie

Mots clés pour faciliter la recherche de cette empreinte

Description de l’empreinte : nom, url datasheet

Nom de l’empreinte affiché

L’empreinte est stockée dans la librairie personnelle « My_Package_Library » par défaut qui se situe par défaut dans « mes documents/KiCad/ ? » ? étant la version de KiCad

Nous retrouvons notre
empreinte dans la librairie

Editions du fichier dans Bloc-notes

Modifier la description et supprimer les liens qui ne correspondent plus

Modifier le mot clé HVSQF8 au lieu de HVSQF6

Sauvegarder

Vous pouvez ici, aussi, modifier les propriétés de l’empreinte si vous ne l’avez pas fait dans l’éditeur de propriétés d’empreinte.

c) Créer une empreinte de A à Z

Clic sur l’éditeur d’empreinte de la fenêtre du PCB pour lancer la fenêtre dédiée

Clic sur l’éditeur d’empreinte du projet pour lancer la fenêtre dédiée

OU

Clic sur créer une nouvelle empreinte

Le composant est vierge

Editer les propriétés de l’empreinte

Donner un nom à l’empreinte dans « value » :
ESP8266_Package

Donner l’adresse de la
« datasheet » :
espressif.com/sites/default/files/d ocumentation/esp8266_hardware _design_guidelines_en.pdf (https://www.espressif.com/sites/default/files/documentation/esp8266_hardware_design_guidelines_en.pdf)

Ne pas modifier la « reference », elle dépend du schéma électrique

Visibilité, taille de la police et couche d’appartenance. Ne pas modifier sauf si nécessaire.

Ne pas oublier pour
enregistrer les
modifications

Choisir CMS

Documentation du composant (il n’y a pas, ici, de directives d’empreinte)

Tracé de la sérigraphie du boitier

- Choix du pas de grille : (ici 0.1mm car les pastilles ont une tailles de 0.25mm

Le pas de grille et la couche de travail

Tracé de la sérigraphie du boitier

- Largeur b = 0.25mm des
pastilles
- Distance inter-pastilles
e = 0.5mm (centre à centre)
- Longueur des pastilles 2xL = 0.8mm
- Longueur et largeur de la pastille centrale
D2 = E2 = 15*0.25 = 3.75mm 15 = 8pastilles + 7 intervalles
- Largeur et longueur du corps du composant
D = E = 4.95mm = 2*0.6 +E2 ou 2*0.6 + D2

Le plus grand multiple
commun des mesures
est 0.05mm. Nous
choisirons la moitié soit
0.025mm

Choisir Forward
Silkscreen pour tracer la
sérigraphie du boitier sur le TOP

Choisir l’outil « tracer ligne »

La couche sérigraphie du dessus doit être visible

Tracer un trait de 4.95mm de hauteur

Choisir l’outil de duplication pour dupliquer la ligne de 5mm (préférer le raccourci « Ctrl + D »

Choisir l’outil de rotation pour tourner de 90° la ligne dupliquée (préférer le raccourci « R »

Raccourcir les 2 côtés de l’angle en haut à gauche.

Ajouter un segment pour indiquer le sens du composant borne

Ajouter un cercle pour indiquer la borne 1 du composant

Création des pastilles

Utiliser la pastille crée pour créer les 31 autres par duplication et rotation

Clic sur les propriétés de la pastille par défaut

Choisir le type de pastille CMS

Choisir un arrondi des pastilles si vous le souhaitez

Selon la documentation du
composant ci-dessus la taille est pastilles est la suivante

X = 025mm et Y = 0.8mm

Laisser le numéro de pastille à 1

Les pastilles commencent à 0.6 du bord et sont espacées de 0.5mm

Choisir l’outil de mesure pour repérer cette distance de 0.6mm

Pas de vernis sur la pastille => masque de vernis

Création du masque pour
le dépôt de la pâte à
braser

Avec l’outil de sélection ,la duplication « Ctrl+D », la rotation « D », la désélection « Ctrl + clic gauche » placer les 24 autres pastilles

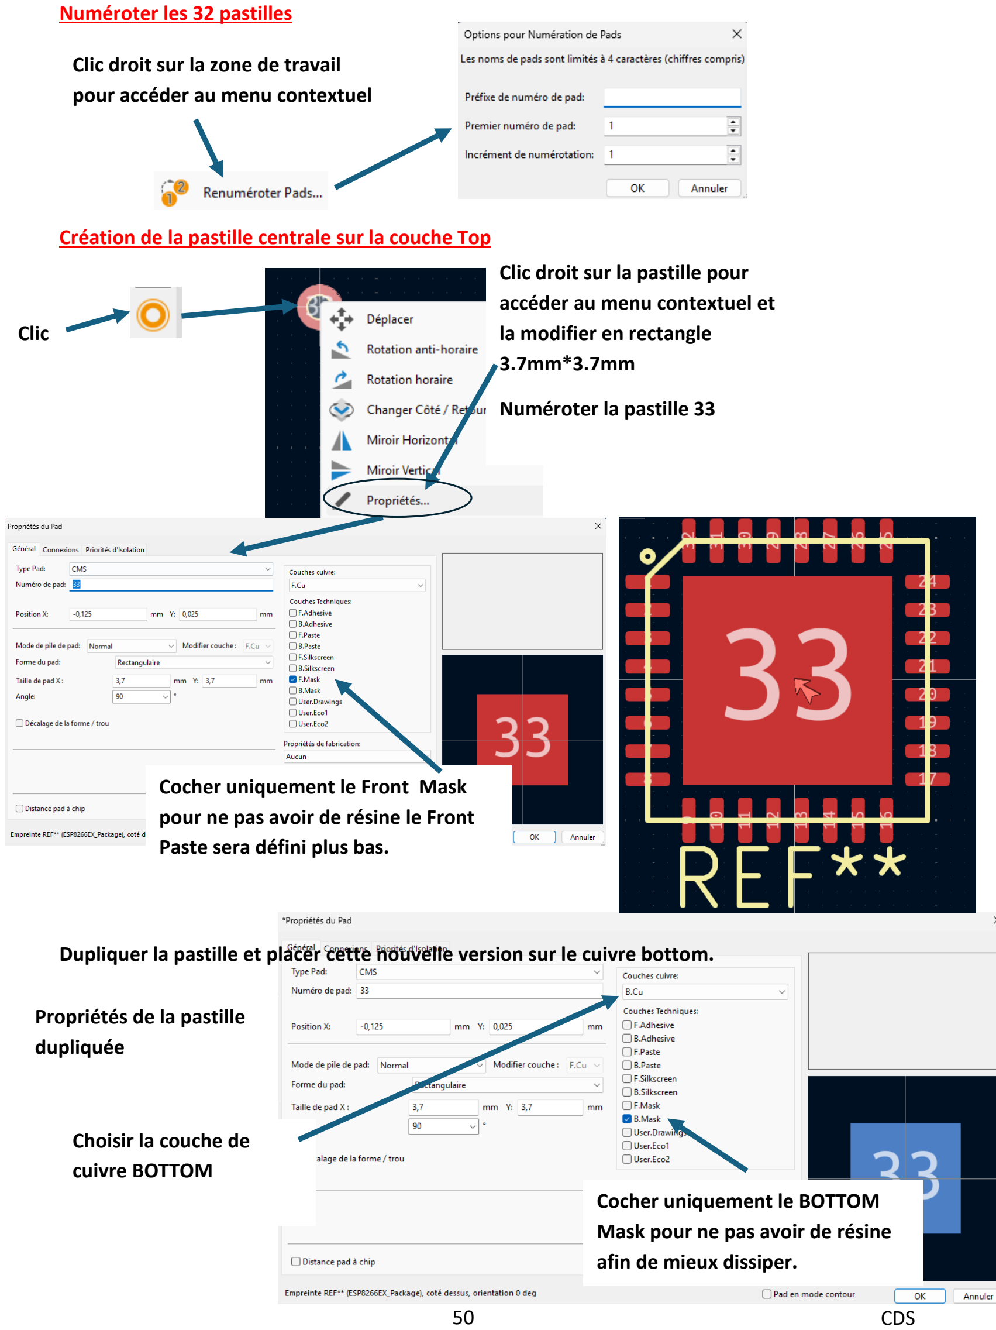
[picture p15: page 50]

Numéroter les 32 pastilles

Création de la pastille centrale sur la couche Top

Dupliquer la pastille et placer cette nouvelle version sur le cuivre bottom.

Clic droit sur la zone de travail pour accéder au menu contextuel

Clic

Clic droit sur la pastille pour accéder au menu contextuel et la modifier en rectangle
3.7mm*3.7mm

Numéroter la pastille 33

Cocher uniquement le BOTTOM Mask pour ne pas avoir de résine afin de mieux dissiper.

Choisir la couche de
cuivre BOTTOM

Propriétés de la pastille
dupliquée

Cocher uniquement le Front Mask pour ne pas avoir de résine le Front Paste sera défini plus bas.

Création de la zone d’exclusion de l’empreinte.

Création de pad thermique pour la diffusion de la chaleur sur la couche bottom

Choisir la couche de travail pour délimiter la zone d’occupation de l’empreinte

Choisir une grille avec un pas de 0.05mm ce qui correspond à environ 2 millièmes de pouce

Choisir l’outil de dessin trait et tracer 4 traits à 0.25mm de l’empreinte soit environ 10 millièmes de pouce.

Clic

Clic droit sur la pastille pour accéder au menu contextuel et la modifier en rectangle
3.7mm*3.7mm

Numéroter la pastille 33

Choisir Pad traversant

Numéro 33

Aucune couche
technique

Choisir Pad
thermique

Diamètre de la
pastille 0.5mm

Diamètre du trou
0.2mm

Résultat avec 25 pads thermiques

Création des emplacements de pâte à braser sur la pastille centrale 33

Définition des emplacements de dépôt de la pâte à braser qui évitent les trous des vias thermiques.
Se placer sur la couche
de la pâte à braser du
dessus

Utiliser l’outil de tracé de polygone pour tracer la zone de base qui sera dupliquée.

Dupliquer et étendre cette zone sur l’ensemble de la
pastille.

Vérifier la validité de l’empreinte créée

21) Listes des sites permettant de télécharger des empreintes
Les fichiers d’empreinte sont de la forme XXXXXX.kicad_mod et sont accessibles :
- Outils du revendeur Mouser : https://www.mouser.fr/electronic-cad-symbols-models/
Mouser Component Search (https://ms.componentsearchengine.com/)
- SnapEda : https://www.snapeda.com/
- SamacSys : https://www.samacsys.com/
- Les sites de revendeur comme Farnell et Radiospares ou digikey https://www.digikey.fr/

### 1. Lancer l’outil de contrôle

d’empreinte

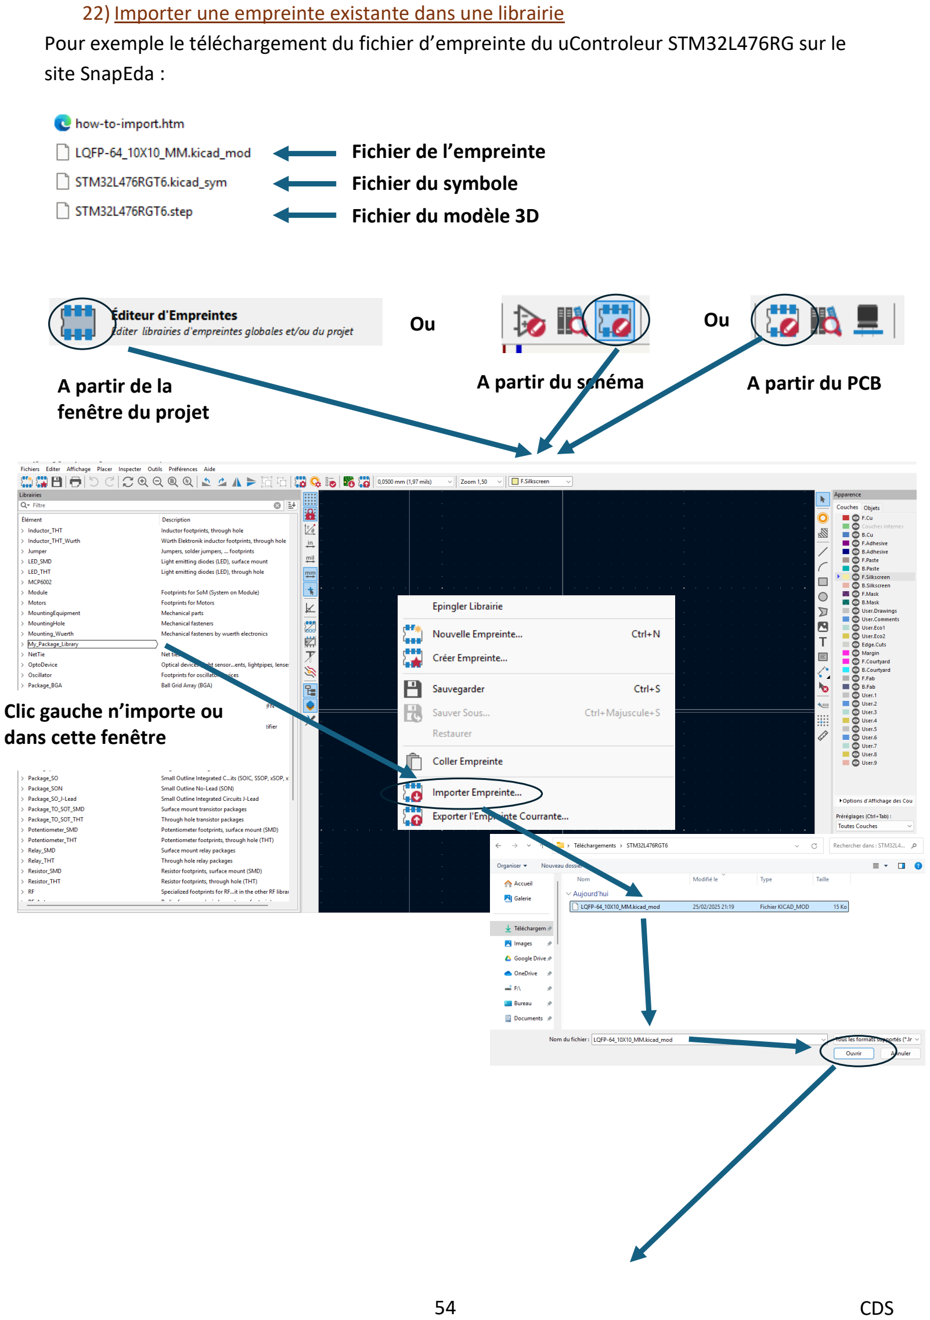
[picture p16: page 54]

22) Importer une empreinte existante dans une librairie
Pour exemple le téléchargement du fichier d’empreinte du uControleur STM32L476RG sur le site SnapEda :

Fichier de l’empreinte
Fichier du symbole
Fichier du modèle 3D

Clic gauche n’importe ou
dans cette fenêtre
Ou | Ou

A partir de la
fenêtre du projet
A partir du schéma | A partir du PCB

23) Déplacer des empreintes d’une librairie à l’autre

Choisir une librairie
(Préférer une de vos
librairies personnelles
pour ne pas perdre les
empreintes à la
prochaine MaJ).

Clic

Vous pouvez créer une
nouvelle librairie si
vous le souhaitez
La nouvelle empreinte apparait maintenant dans la liste d’empreintes de ma librairie « My_Package_Library »

2.Clic droit sur
l’empreinte à coller ou
à déplacer

3.Choisir
l’action à
réaliser

4.Sélectionner
la librairie de
destination

5.clic

Ou | Ou

A partir de la
fenêtre du projet
A partir du schéma | A partir du PCB

24) Déplacer plusieurs empreintes d’une librairies à l’autre
Copier tous les fichiers empreintes voulus dans le répertoire de la librairie cible (fichiers .kicad_mod).
25) Modifier ou compléter les propriétés d’une empreinte

Nom de l’empreinte dans la librairie

Mots clés pour faciliter la recherche de cette empreinte

Description de l’empreinte : nom, url datasheet,…..

Nom de l’empreinte affiché

Sauvegarder les modifications pour convenir à la nouvelle empreinte

Donner l’URL de la datasheet

Description de l’empreinte visible sur le PCB

Ou | Ou

A partir de la
fenêtre du projet
A partir du schéma | A partir du PCB

Choisir la librairie et
le nom de
l’empreinte

Editer les propriétés
de l’empreinte

26) Librairies et fichiers empreintes
Exemple de librairie personnelle « My_Package_Library »

Listes des fichiers empreintes de la librairie

Editions du fichier « HVSOF8_THERM »dans Bloc-notes

Description et liens de la datasheet

Mot clé HVSOF8

Vous pouvez ici, aussi, modifier manuellement les propriétés de l’empreinte si vous ne l’avez pas fait dans l’éditeur de propriétés d’empreinte.

La librairie est un répertoire dont le nom fini par « .pretty »

27) Gestions des librairies d’empreinte
a) Emplacement des librairies et généralités Les librairies de base de Kicad se situent par défaut :

Les librairies personnelles ou propre au projet se situent par defaut :

Ne pas utiliser ou créer des librairies dans « Documents » si vous souhaitez une portabilité du projet.

(Voir Portabilité des librairies page 64)

b) Configurer les librairies :

Chemins de substitution déjà créés. Ils permettent de raccourcir les chemins affichés ci-dessus (ils ne permettent pas la portabilité du projet)

Examinateur de librairies d’empreintes.
Permet de visionner les symboles des librairies mais pas de configurer les librairies.

c) Les librairies personnelles globales
Les librairies personnelles globales sont des "librairies globales" crées par l’utilisateur.

Les librairies personnelles globales peuvent être utilisées dans plusieurs projets mais sont rattachées au profil utilisateur d’un PC ce qui empêche toute portabilité. Les fichiers de déclaration se trouvent dans ce répertoire.

Les fichiers qui contiennent les emplacements des "librairies globales" (KiCad + personnelles) sont :
- sym-lib-table pour les librairies de symboles globales
- fp-lib-table pour les librairies d’empreintes globales

Alors que les "librairies spécifiques au projet" sont déclarées dans des fichiers propres au projet et peuvent l’accompagner dans sa diffusion.

Dans le répertoire du projet nous trouvons les fichiers qui contiennent les emplacements des librairies spécifiques au projet :
- sym-lib-table pour les librairies de symboles personnelles
- fp-lib-table pour les librairies d’empreintes personnelles
d) Création d’une librairie
Après téléchargement des fichiers, le fichier correspondant à l’empreinte se termine avec

Exemple de création de "librairie globale" (les "librairies spécifiques" sont créées de la même façon mais ne se trouvent pas au même endroit (voir plus loin la portabilité))

1.Créer un répertoire dans
le répertoire de KiCad
perso, dans « Documents »
-- « footprints » pour une librairie globale

Cette façon de faire est non portable mais fonctionne
très bien sur un poste de
travail

4.La librairie apparait
maintenant dans la liste des librairies.

e) Configuration des chemins
Les chemins ne fonctionnent que si vous travaillez sur un poste dédié => pas de portabilité possible car les chemins sont enregistrés dans les fichiers fp-lib-table et sym-lib-table du profil utilisateur.

Voici l’arborescence qui est proposée pour plusieurs projets :

Voici l’arborescence qui est proposée pour un seul projet :

A partir des arborescences des projet nous définissons des chemins relatifs ou absolus vers
les librairies
Pour l’arborescence multi projets | Déclarer les chemins en relatifs ou en absolus des
| librairies personnelles et leur donner un nom.
| Pour accéder au dossier parent du projet en relatif : ../
| ../ : Ne fonctionne pas pour les librairies de symboles sur KiCad9

Déclarer vos librairies personnelles de symboles avec un chemin relatif :

Le chemin relatif ../ pour la librairie de symbole n’est pas fiable. Il faut passer par le chemin prédéfini dans KiCad ${KIPRFMOD} qui pointe le répertoire du projet :
${KIPRJMOD}/../libs/Models/librairie_global_perso

Déclarer vos librairies personnelles d’empreinte :

Par exemple pour accéder à la librairie My_Package_Library : ${MY_FOOTPRINTS_DIR} / My_Package_Library
qui utilise le chemin relatif défini précédemment.

Autre solution
Il est possible d’utiliser le chemin prédéfini dans KiCad ${KIPRFMOD} : ${KIPRJMOD}/../libs/footprints/My_Package_Library

Pour l’arborescence mono projet présentée précédemment

Déclarer les chemins relatifs des librairies personnelles et leur donner un nom.

Pour accéder au dossier du projet : ./

Déclarer vos librairies personnelles de symboles avec un chemin relatif :

Par exemple pour accéder à la librairie_global_perso : ${KIPRJMOD}/libs/symbols/librairie_global_perso
qui utilise le chemin prédéfini de KiCad ${KIPRJMOD} qui pointe le répertoire du projet
Ou
${MY_MODELS_DIR} /librairie_global_perso
Qui utilise le chemin relatif défini précédemment

Déclarer vos librairies personnelles d’empreinte avec un chemin relatif :

Par exemple pour accéder à la librairie My_Package_Library : ${KIPRJMOD}/libs/footprints/My_Package_Library
qui utilise le chemin prédéfini de KiCad ${KIPRJMOD} qui pointe le répertoire du projet
Ou
${MY_FOOTPRINTS_DIR} / My_Package_Library
qui utilise le chemin relatif défini précédemment f) Gestion des librairies pour la portabilité de projet
Ceci est une proposition permettant de simplifier tous les problèmes de liens entre les librairies spécifiques de votre PC et le projet que vous souhaitez partager.

Voici l’arborescence qui est proposée pour plusieurs projets :

A partir de ces arborescences nous allons définir des chemins relatifs vers les "librairies spécifiques" contenu dans le dossier "libs" du dossier "Projets KiCad"

Configuration des librairies de symboles spécifiques au projet

Configuration des librairies d'empreintes spécifiques au projet

Dans le répertoire du projet nous trouvons les fichiers qui contiennent les emplacements des librairies spécifiques au projet :
- sym-lib-table pour les librairies de symboles personnelles
- fp-lib-table pour les librairies d’empreintes personnelles

Contenu de sym-lib-table

Contenu de fp-lib-table

Modifier le chemin des librairies pour passer avec des chemins relatifs

Le chemin prédéfini dans KiCad ${KIPRFMOD} pointe le répertoire du projet :

Modifier le chemin des librairies pour passer avec des chemins relatifs

Le chemin prédéfini dans KiCad ${KIPRFMOD} pointe le répertoire du projet : ${KIPRJMOD}/../libs/footprints/My_Package_Library.pretty

28) Création de plan de masse
a) Plan de masse global | 1. Clic sur tracer une zone remplie

### 2. Clic gauche sur un des coins de la

| zone à dessiner La fenêtre suivante s’ouvre.

Choisir la couche du
plan de masse

Choisir le potentiel
relié au plan de masse

Donner un nom au plan
de masse

Choisir avec ou sans
frein thermiques ainsi
que la taille des freins
thermiques

Autoriser ou non les ilots

3. Remplir les champs de cette fenêtre.

### 4. clic gauche à chaque coin du plan de masse et finir sur le premier

angle pour fermer le dessin

Pour enregistrer

Exemple ci contre de frein thermique. Les freins thermiques permettent la montée en température de la soudure sans avoir besoin de monter en température tout le plan.

### 5. Presser la touche B pour rafraichir l’écran

b) Plan de masse local
Reprendre les étapes 1, 2, 3, 4 et 5 précédentes pour délimiter une zone locale avec un autre mode de fonctionnement.

Exemple avec frein thermique général sur l’ensemble du plan transformée localement sur une zone sans frein thermique

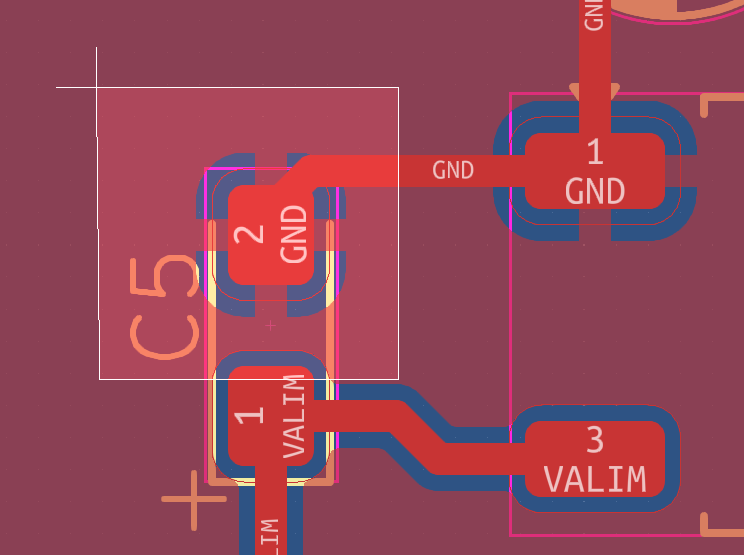
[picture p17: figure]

29) Ajouter du texte ou des images par sérigraphie
a) Ajout de texte
b) Ajout d’image
- Transformer votre image ou photo en Bmp monochrome. Par exemple avec le logiciel paint sur windows
- Lancer le convertisseur d’image de KiCad accessible dans le projet

•

Clic sur cette icône pour ajouter du texte

1)Ecrire le texte ici texte

2)Choisir la couche de la
sérigraphie en face avant : F.Silkscreen

3)Choisir la police de
caractère

4)Dimension des caractères

5)Orientation du texte

1) Ouvrir le fichier image
2) Redimmensionner
votre image au besoin
3) Choisir « Empreinte
KiCad » et la couche de
sérigraphie du dessus
4) Exporter dans le
presse papier

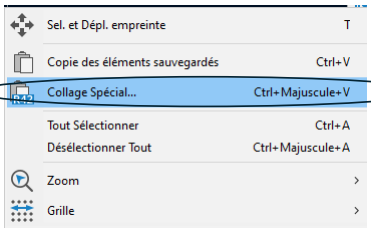
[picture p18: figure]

5) Clic droit sur le PCB
6) Clic droit puis « collage spécial »

30) Génération des fichiers de fabrication (Fichiers GERBER)
a) Génération des fichiers des différentes couches

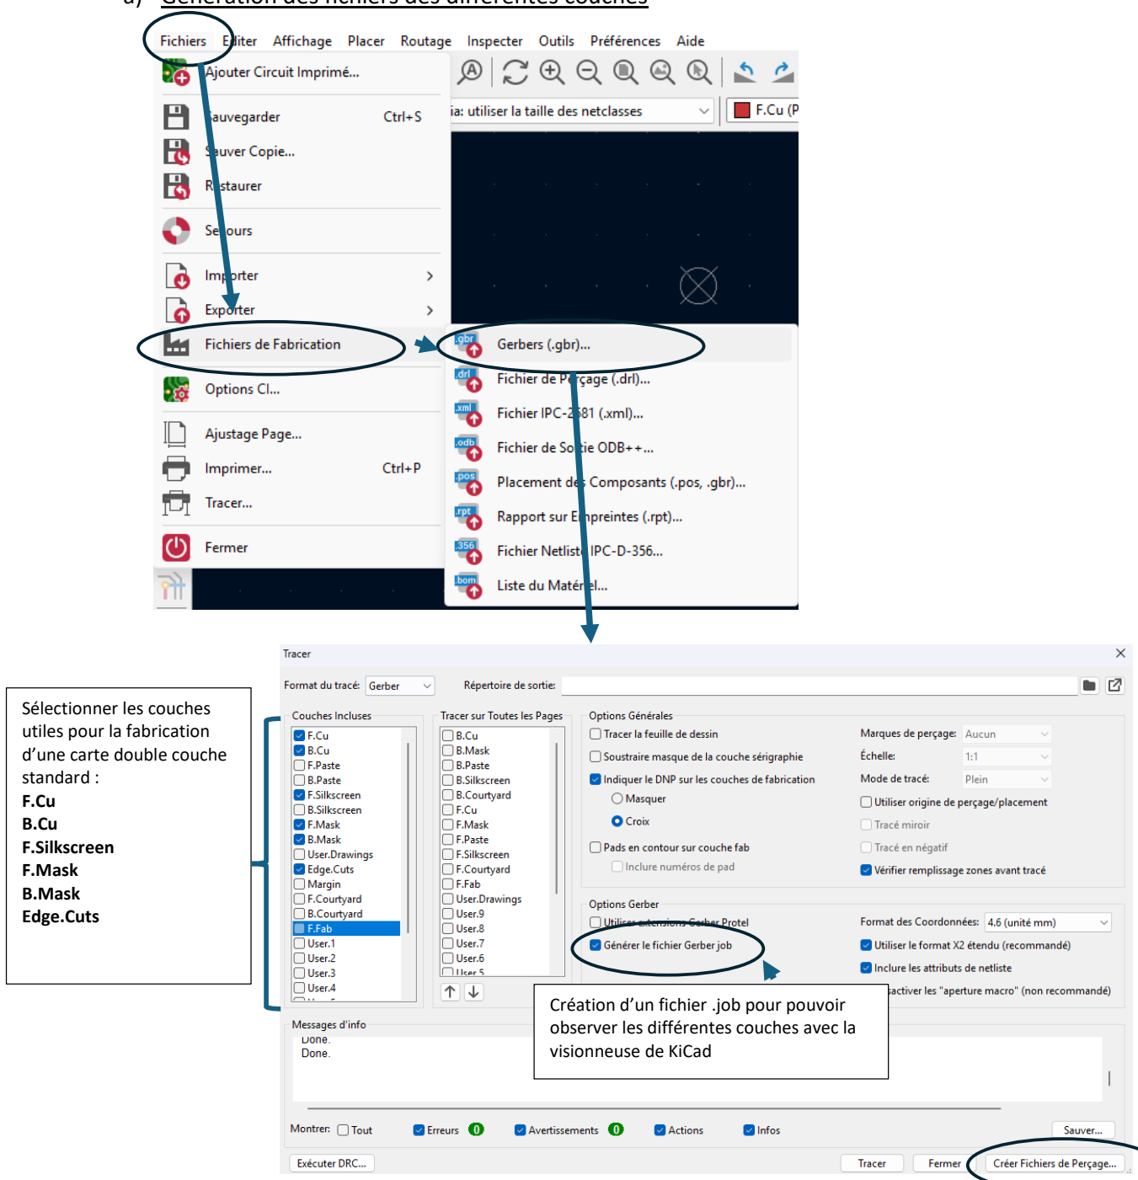
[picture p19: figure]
Sélectionner les couches utiles pour la fabrication d’une carte double couche standard : F.Cu B.Cu F.Silkscreen F.Mask B.Mask Edge.Cuts; Création d’un fichier .job pour pouvoir; visionneuse de KiCad

F.Cu : Front Cuivre (emplacement du cuivre sur le dessus)
B.Cu : Bottom Cuivre (emplacement du cuivre sur le dessous)
F.Paste : Front Paste (Nécessaire pour la fabrication du pochoir pour le dépôt de pate à braser sur le dessus) B.Paste : Bottomt Paste (Nécessaire pour la fabrication du pochoir pour le dépôt de pate à braser sur le dessous) F.SilkScreen : Front SilkScreen (Sérigraphie du dessus)
B.SilkScreen : Bottom SilkScreen (Sérigraphie du dessous)
F.Mask : Front Mask (Emplacement du vernis sur le dessus)
B.Mask : Bottom Mask (Emplacement du vernis sur le dessous) Edge.Cuts : Détourage de la carte

observer les différentes couches avec la

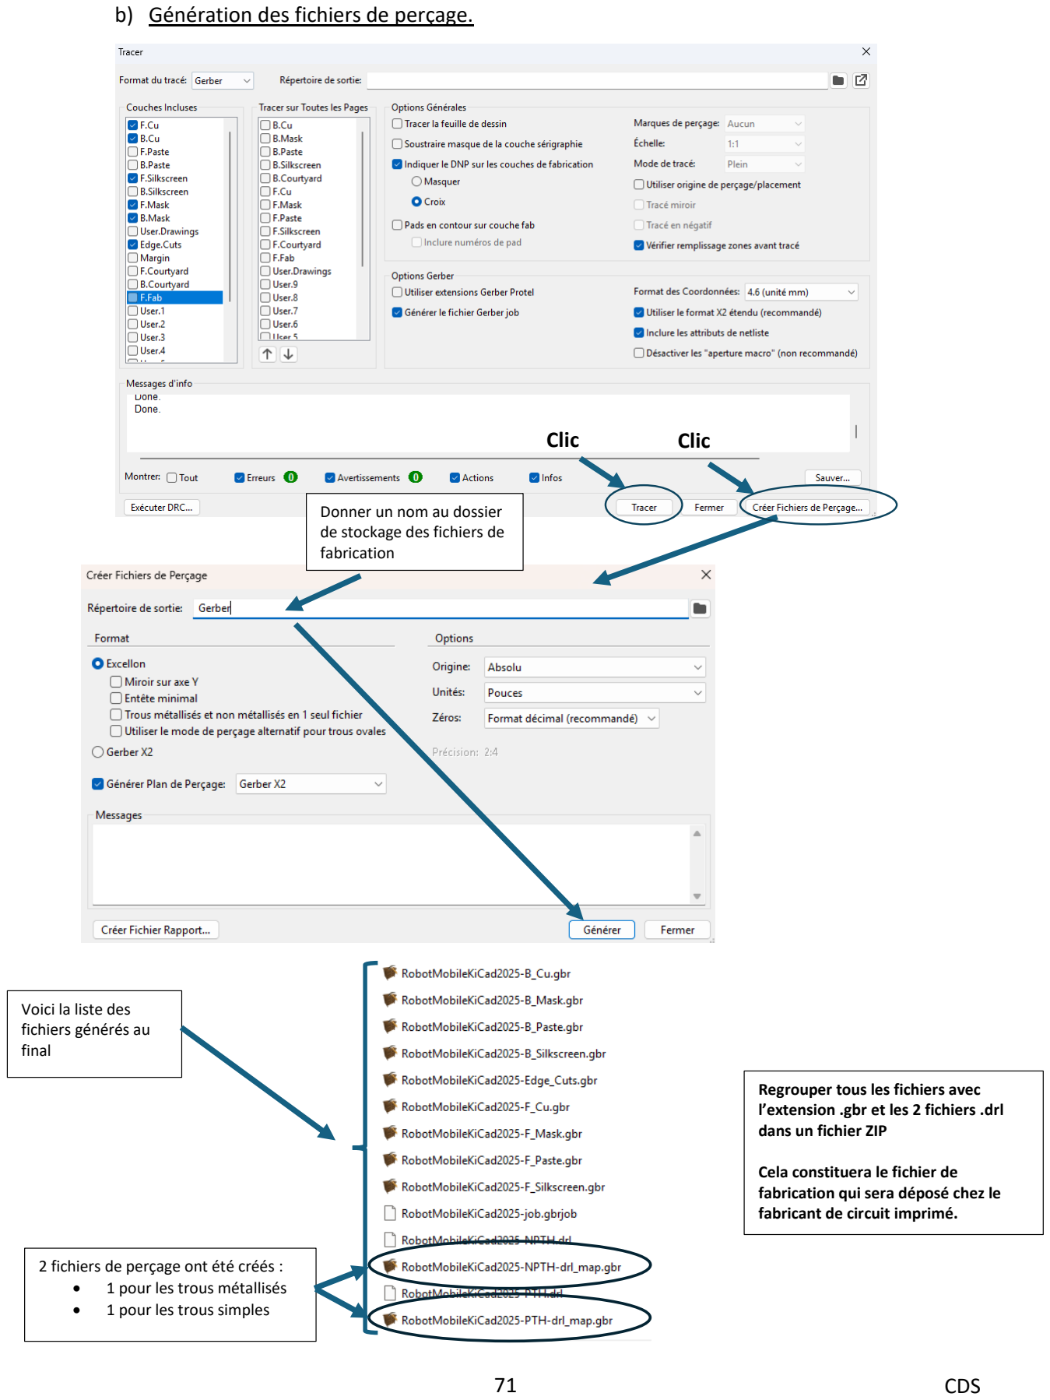
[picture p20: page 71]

b) Génération des fichiers de perçage.

Clic

Donner un nom au dossier
de stockage des fichiers de fabrication

Voici la liste des
fichiers générés au
final

Regrouper tous les fichiers avec l’extension .gbr et les 2 fichiers .drl dans un fichier ZIP

Cela constituera le fichier de fabrication qui sera déposé chez le fabricant de circuit imprimé.

2 fichiers de perçage ont été créés :
- 1 pour les trous métallisés
- 1 pour les trous simples

Clic

c) Visionnage des différentes couches de fabrication

Pour ajouter les trous métallisés et non métallisé dans la visionneuse :

Lancer la visionneuse

L’ensemble des couches
sélectionnées apparait ici

Cocher la ou les
couches à afficher

## IV. Modèle 3D du composant

1) Déposer le fichier modèle 3D dans la librairie
Le fichier modèle 3D est un fichier avec une extension .step ou .stp

Placer ce fichier dans le répertoire de votre librairie 3D qui se trouve par défaut :

2) Associer un modèle 3D avec une empreinte

Clic sur le gestionnaire
d’empreintes

1.Sélectionner
l’empreinte concernée

2.Puis choisir d’éditer les propriétés de l’empreinte.

Clic

La suite page suivante

Créer un nouveau chemin pour indiquer ou se trouve vos
modèles 3D. je le nomme :
KICAD9_MY_3DMODEL_DIR

A faire uniquement si
le chemin de votre
librairie n’a pas été
créé

Le chemin vers la
librairie est créé.
Clic pour choisir le
modèle 3D

A faire uniquement si vous n’avez pas défini le ou les chemins vers le répertoire de vos modèles 3D et si vous n'avez pas besoin de la portabilité du projet

Clic pour définir le
chemin

1.Choisir le chemin vers la librairie

2.Choisir le modèle 3D

3.Clic

Le modèle 3D n’est pas placé comme il faut vis-à-vis de son empreinte.

Modifier les rotations
pour le placer
correctement et
notamment vis-à-vis du
détrompeur

Clic

Simulations du projet

libs

Projet1P

Projet2P

Dossier Projets KiCad

Simulations du projet

Documentation technique

Documentation technique

3) Portabilité des modèles 3D

Voici l’arborescence qui est proposée pour plusieurs projets :

A partir de ces arborescences nous allons définir des chemins relatifs vers les modèles 3D contenus dans le dossier "libs" du dossier "Projets KiCad"

Le chemin du modèle 3D est modifié pour passer en relatif

../libs/3dmodels/Condensateur_film.step

Ce chemin permet à partir du répertoire projet de remonter d'un cran "../" puis de pointer le fichier Condensateur_film.step dans le répertoire "libs/3dmodels"

Les modèles 3D sont
stockés ici

4) Liste des sites permettant de télécharger les modèles 3D
Les fichiers de modèle 3D sont de la forme XXXXXX.kicad_mod et sont accessibles :
- Outils du revendeur Mouser : https://www.mouser.fr/electronic-cad-symbols-models/
Mouser Component Search (https://ms.componentsearchengine.com/)
- SnapEda : https://www.snapeda.com/
- SamacSys : https://www.samacsys.com/
- Les sites de revendeur comme Farnell et Radiospares ou digikey https://www.digikey.fr/
- Recent models | 3D CAD Model Collection | GrabCAD Community Library (https://grabcad.com/library)

## Simulations

1) Généralités
Menu « preferences » choisir « preferences »

Ne pas oublier de
cocher les cases pour
autoriser l’affichage des
valeurs des tensions et
courants des points de
fonctionnement DC

Les composants utiles à la simulation se trouvent dans la librairie « simulation_spice » ou « pspice ». La plupart des paramètres intrinsèques au composant sont modifiables dans les propriétés de celui ci.

2) Modèles de simulation et librairies de simulation personnelles Les librairies personnelles de simulation se trouve par défaut dans :
a) Les librairies téléchargeables
Des librairies de composants sont à disposition sur github :
GitHub - kicad-spice-library/KiCad-Spice-Library: Centralized repo to store KiCad/Spice modules for simulations (https://github.com/kicad-spice-library/KiCad-Spice-Library/tree/master)

Par exemple, téléchargeons la librairie « DIODE2 » et plaçons la dans notre répertoire
« Models ». Cette librairie est un fichier texte avec une extension .lib qui contient plusieurs centaines de références de diodes. Cette librairie est accessible dans les propriétés des composants dans « simulation model » (voir plus loin pour l’utilisation)

Extrait de DIODE2.lib

b) Créer un modèle de simulation
Télécharger un modèle de simulation sur internet.
Par exemple le modèle de simulation de la diode Schottky VS-E5TX3006-M3 de chez VISHAY. Télécharger la documentation constructeur : https://www.vishay.com/docs/96754/vs-e5tx3006-m3.pdf
Page 5 de cette documentation nous trouvons le lien vers le modèle SPICE de cette diode http://www.vishay.com/doc?96918

Avec un éditeur de texte classique, copier/coller dans un fichier texte cette partie :

Si vous pensez utiliser ce fichier pour placer d’autres modèles de simulation, vous pouvez réduire l’encombrement en l’écrivant sur une seule ligne :

.MODEL E5TX3006 D IS=25.000E-6 N=3.0704 RS=3.6946E-3 IKF=.47806 CJO=432.45E-12 M=.40823 VJ=.3905 ISR=1.0010E-15 NR=4.9950 BV=700.16 IBV=2.5912 TT=24.089E-9 FC=0.2 XTI=2
ou

.MODEL E5TX3006 D (IS=25.000E-6 N=3.0704 RS=3.6946E-3 IKF=.47806 CJO=432.45E-12 M=.40823 VJ=.3905 ISR=1.0010E-15 NR=4.9950 BV=700.16 IBV=2.5912 TT=24.089E-9 FC=0.2 XTI=2)

Remarque : Si vous allez à la ligne au cours de la description il faut ajouter un « + » en début de chaque ligne

Enregistrer ce fichier texte au nom du composant avec une extension « .lib ».

c) Créer une librairie à partir d’un modèle de simulation.
Suivre la procédure du b) puis enregistrer le fichier avec non pas le nom du composant mais le nom que vous avez choisi pour votre librairie.
d) Ajouter un modèle dans une librairie
Il suffit pour cela d’ajouter, avec un éditeur de texte, une ligne supplémentaire correspondant à votre model.

L’image ci-dessus correspond à 9 modèles de simulation de diodes dans la librairie DIODE2.lib

3) Point de fonctionnement DC

Placer les
composants
nécessaires

La source de tension
continue se nomme
« VDC »

Plusieurs façons de dessiner un schéma électrique. Le symbole de GND est nécessaire pour fixer le 0V.

### 1. Lancer le simulateur

### 2. Lancer la simulation

### 3. Choisir point de

fonctionnement DC

### 2. Choisir le mode de compatibilité en fonction des modèles de simulation

que vous utilisez

### 3. Clic

4) DC SWEEP (Balayage simple-> Une seule courbe) Exemple caractéristique I(V) de la diode E5TX3006
a) Voir le paragraphe 2) pour les modèles de simulation
b) Dessiner le schéma de simulation

### 4. Clic pour lancer les calculs de

l’analyse précédemment créée

Voici les résultats

La diode est une diode classique ou schottky, cela n’a pas d’importance pour la simulation car nous allons utiliser un modèle de simulation spécifique.

Le plus simple est de prendre la diode « D » dans la librairie « simulation_SPICE »

L’alimentation est un « VDC » dans la librairie de composants « simulation_SPICE »

Le GND est obligatoire pour fixer la référence 0V à un endroit du circuit.

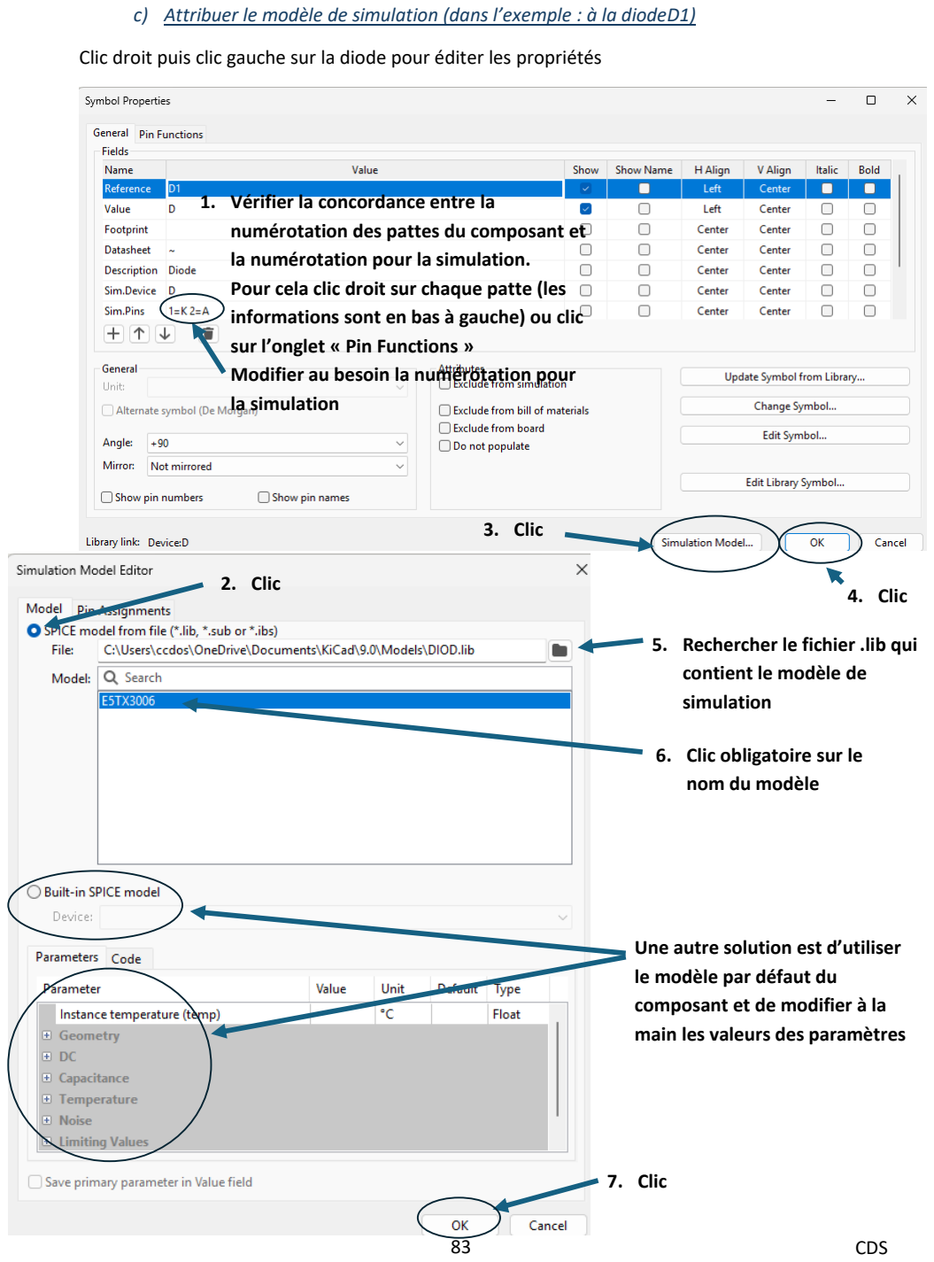
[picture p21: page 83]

c) Attribuer le modèle de simulation (dans l’exemple : à la diodeD1)

Clic droit puis clic gauche sur la diode pour éditer les propriétés

### 1. Vérifier la concordance entre la

numérotation des pattes du composant et la numérotation pour la simulation.
Pour cela clic droit sur chaque patte (les informations sont en bas à gauche) ou clic sur l’onglet « Pin Functions »
Modifier au besoin la numérotation pour la simulation

### 3. Clic

### 2. Clic

### 5. Rechercher le fichier .lib qui

contient le modèle de
simulation

### 6. Clic obligatoire sur le

nom du modèle

### 7. Clic

Une autre solution est d’utiliser le modèle par défaut du
composant et de modifier à la main les valeurs des paramètres

### 4. Clic

Dossier projet

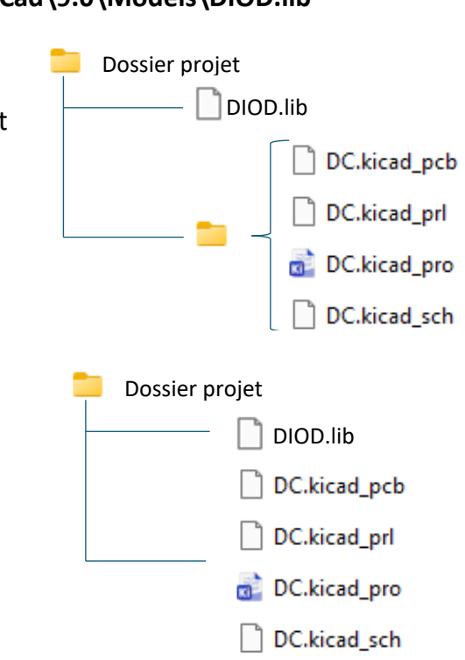
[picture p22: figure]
Dossier projet; DIOD.lib

libs | Models | DIOD.lib
d) Modèle de simulation portable(optionnel)

Si vous souhaitez distribuer votre projet de simulation vous allez vous buter sur le problème de portabilité des librairies utilisées. Une solution est de fournir la librairie de simulation dans votre dossier de projet.

Cela impose de fournir un chemin relatif lors de la déclaration du modèle de simulation.

A la place de : C:\Users\ccdos\OneDrive\Documents\KiCad\9.0\Models\DIOD.lib

Utiliser par exemple :

- ..\DIOD.lib si la librairie est dans le dossier parent
- DIOD.lib si la librairie est dans le même dossier
- ..\libs\Models\DIOD.lib si la librairie est dans un autre dossier
e) Paramétrer la simulation

### 1. Clic

### 2. Clic

### 3. Choisir « DC Sweep

Analysis »

### 4. Clic

### 5. Choisir le type d’analyse

Ici V pour effectuer un balayage en tension

### 6. Choisir la source à

faire varier

7. Choisir la valeur de départ, la valeur finale et le pas
(Dans cet exemple :
variation de V1 de 0 à 2V
par pas de 0.1V) | 8. Clic

f) Exploiter les résultats de la simulation

Choisir la courbe à observer (ici I(D1))

Choisir 1 ou 2
curseurs pour
effectuer des
mesures

Coordonnées du
point de mesure
curseur

Pour ajouter des courants dans la liste en haut à droite. Cliquer sur la patte du composant (le courant est pris positif rentrant)

Pour ajouter des potentiels dans la liste en haut à droite. Cliquer sur un fil

5) DOUBLE DC SWEEP (Double Balayage-> Réseau de caractéristiques)
Exemple caractéristiques ID(VDS) pour plusieurs valeurs de VGS dans le cadre de l’étude d’un transistor MOS Canal N
a) Voir le paragraphe 2) pour les modèles de simulation
b) Dessiner le schéma de simulation
c) Attribuer le modèle de simulation (dans cette exemple : au transistor NMOS)

Clic droit puis clic gauche sur le transistor pour éditer les propriétés

Le transistor NMOS est un transistor générique de la librairie « Simulation_SPICE », cela n’a pas d’importance pour la simulation car nous allons utiliser un modèle de simulation spécifique.

Les alimentations sont des « VDC » dans la librairie de composants « simulation_SPICE »

Le GND est obligatoire pour fixer la référence 0V à un endroit du circuit.

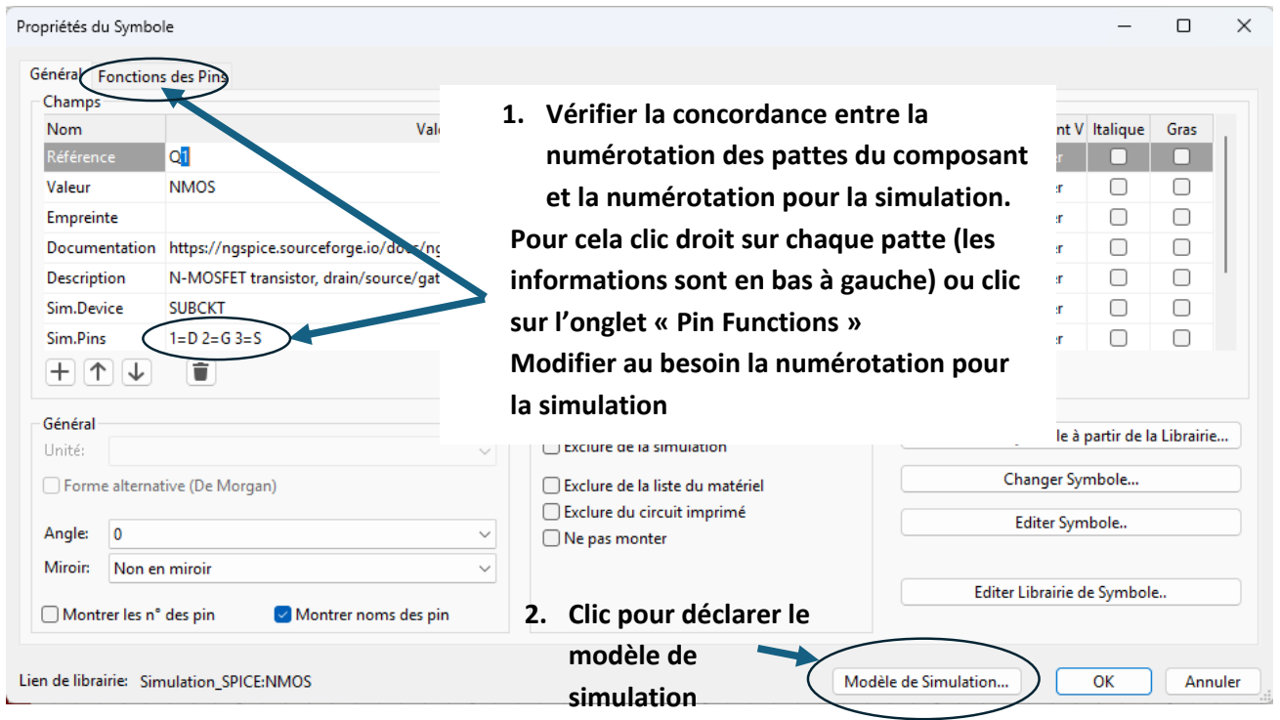
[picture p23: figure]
1. Vérifier la concordance entre la numérotation des pattes du composant et la numérotation pour la simulation.; sur l’onglet « Pin Functions » Modifier au besoin la numérotation pour la simulation; 2. Clic pour déclarer le modèle de simulation

Pour cela clic droit sur chaque patte (les informations sont en bas à gauche) ou clic

Voir page suivante

Clic

### 5. Clic gauche obligatoire sur le

nom du modèle pour le
sélectionner

### 6. Clic

Une autre solution est d’utiliser le modèle par défaut du composant et de modifier à la main les valeurs des paramètres

### 3. Rechercher le fichier .lib qui

contient le modèle de
simulation

### 4. Modifier le chemin du fichier

avec un chemin relatif pour la portabilité (voir d)

Dossier projet

Dossier projet; DIOD.lib

libs | Models | DIOD.lib
d) Modèle de simulation portable(optionnel)

Si vous souhaitez distribuer votre projet de simulation vous allez vous buter sur le problème de portabilité des librairies utilisées. Une solution est de fournir la librairie de simulation dans votre dossier de projet.

Cela impose de fournir un chemin relatif lors de la déclaration du modèle de simulation.

A la place de : C:\Users\ccdos\OneDrive\Documents\KiCad\9.0\Models\DIOD.lib

Utiliser par exemple :

- ..\DIOD.lib si la librairie est dans le dossier parent
- DIOD.lib si la librairie est dans le même dossier
- ..\libs\Models\DIOD.lib si la librairie est dans un autre dossier

e) Paramétrer la simulation

### 1. Clic

### 2. Clic

### 3. Choisir « DC Sweep

Analysis »

### 4. Clic

### 5. Choisir le type d’analyse

Ici V pour effectuer un balayage en tension

### 6. Choisir la source à faire

varier (Ici V2
correspond à VDS)
7. Choisir la valeur de départ, la valeur finale et le pas (Dans cet exemple :
variation de V1 de 0 à
600mV par pas de 10mV)

### 9. Clic

### 8. Cocher source 2 pour tracer un réseau de

caractéristiques. V2 correspond dans notre cas à la tension VGS (Dans cet exemple : variation de V2 de

### 3 à 5V par pas de 100mV)

### 2. Clic

OU

f) Exploiter les résultats de la simulation

Remarque : Pour les mesures curseurs, il est impossible de choisir la courbe sur la version
9.0.4. Privilégier le zoom pour lire les valeurs (Molette de la sourie ou outils de zoom)

Choisir la courbe à observer (ici I(D1))

Choisir 1 ou 2
curseurs pour
effectuer des
mesures

Coordonnées du
point de mesure
curseur

Pour ajouter des courants dans la liste en haut à droite. Cliquer sur la patte du composant (le courant est pris positif rentrant)

Pour ajouter des potentiels dans la liste en haut à droite. Cliquer sur un fil

### 1. Lancer la simulation

6) Temporelle avec sinus
Exemple détermination de la tension VBR de la diode E5TX3006
a) Voir le 2) pour les modèles de simulation
b) Dessiner le schéma de simulation
c) Attribuer le modèle de simulation à la diode

Voir V.4)c)

d) Paramétrer la simulation

La diode est une diode classique, cela n’a pas d’importance pour la simulation car nous allons utiliser un modèle de simulation spécifique.

Le plus simple est de prendre la diode « D » dans la librairie « simulation_SPICE »

L’alimentation est un « VSIN » dans la librairie de composants « simulation_SPICE »

Les paramètres sont : tension moyenne 0V (dc=0), amplitude de 800V (ampl=800) et fréquence de 10kHz (f=10k) (ac=1 n’est pas utile pour l’analyse temporelle).

Le GND est obligatoire pour fixer la référence 0V à un endroit du circuit.

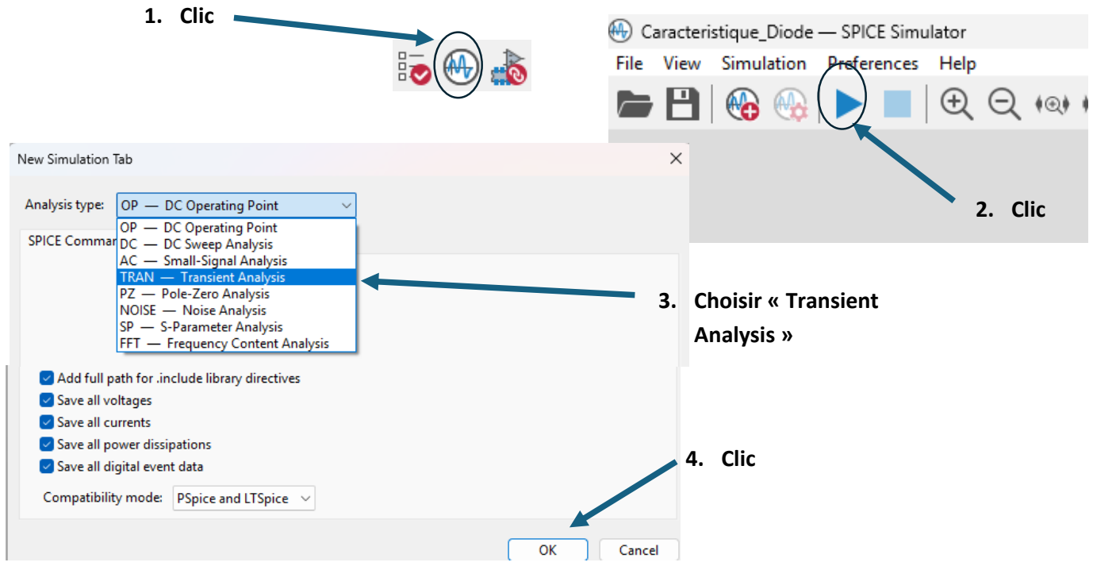
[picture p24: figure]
1. Clic; 2. Clic; 3. Choisir « Transient Analysis »; 4. Clic

e) Exploiter les résultats de la simulation

Nous souhaitons observer VD1 et ID1 pour mesurer la valeur de VBR (Tension de diode inverse maximale au delà de laquelle la diode conduit en inverse (destruction de la diode))

### 5. Choisir l’espace temporel

entre 2 points de la courbe (ici 100points par période car la période est de 100us et l’espace entre 2 points est de 1us)
6. Donner le temps de fin de simulation. Nous ferons une simulation sur 10 périodes pour détecter d’éventuels régimes transitoires.
10x100us = 1ms

### 7. Clic

La courbe du courant ID1 est accessible mais seules les courbes des potentiels de la cathode et de l’anode sont accessibles et non VD1

La tension de diode VD1 est la différence de potentiel entre l’anode et la cathode. Pour la créer cliquer sur l’icone
suivante

### 2. Faire la différence des

potentiels d’anode et de
cathode en reprenant leur
nom exact à droite du
graphe.

### 1. Clic pour

ajouter une

### 3. La tension de la diode VD1 est alors

accessible. Cliquer sur « plot » et « cursor 1 » pour effectuer la mesure de tension.

### 4. Cliquer sur « plot » du courant ID1

### 5. Zoomer sur une période en maintenant

le clic gauche à l’endroit où se trouve le curseur (bien englober la totalité du signal sur la période).

### 7. Déplacer le curseur de tension

de VD1 à en concordance
temporelle avec le départ du courant négatif.

### 6. Noter la valeur de

tension du curseur

7) Temporelle avec impulsion
Exemple mesure du temps de recouvrement avec la diode E5TX3006
a) Voir le 2) pour les modèles de simulation
b) Dessiner le schéma de simulation
c) Attribuer le modèle de simulation à la diode

Voir V.4)c)

d) Paramétrer la simulation

Voir V.5)d) (Attention au temps de simulation (10 périodes suffisent) et au pas de simulation (au moins 100points par période)

e) Exploiter les résultats de la simulation

Nous souhaitons observer VD1 et ID1 diode

La diode est une diode classique, cela n’a pas d’importance pour la simulation car nous allons utiliser un modèle de simulation spécifique.

Le plus simple est de prendre la diode « D » dans la librairie « simulation_SPICE »

L’alimentation est un « VPULSE » dans la librairie de composants « simulation_SPICE »

Les paramètres sont : Tension min (y1=-300V), tension max (y2=+300V), temps de retard avant que le signal commence à croitre (td=10ns), temps de montée (tr=100ns), temps de descente (tf=100ns), temps à la valeur max (tw=4us), période (per=8.4us)

Le GND est obligatoire pour fixer la référence 0V à un endroit du circuit.

La courbe du courant ID1 est accessible mais seules les courbes des potentiels de la cathode et de l’anode sont

La tension de diode VD1 est la différence de potentiel entre l’anode et la cathode. Pour la créer cliquer sur l’icone
suivante

### 1. Faire la différence des

potentiels d’anode et de
cathode en reprenant leur
nom exact à droite du
graphe.

### 3. La tension de la diode VD1 est alors

accessible. Cliquer sur « plot » et « cursor 1 » pour effectuer la mesure de tension.

### 4. Cliquer sur « plot » du courant ID1

### 5. Zoomer sur le recouvrement

(Maintient clic gauche sur une zone)

### 6. Utiliser les curseurs pour

effectuer les mesures

### 2. Clic pour

ajouter une
courbe

8) Fréquentielle
Exemple : Réponse fréquentielle d’un amplificateur inverseur
a) Voir le 2) pour les modèles de simulation
b) Dessiner le schéma de simulation
c) Attribuer le modèle de simulation à l’AOP

Voir V.4)c) et d) (Préférez la portabilité de votre projet)

d) Paramétrer la simulation

N’importe quelle source de tension de la librairie « Simulation_SPICE » convient. Il faut simplement, dans les propriétés de la source, ajouter « ac=1 ». Le fait d’ajouter cette propriété permet au simulateur de fixer la tension d’entrée (tension de référence pour les calculs)

L’amplificateur est ici un amplificateur de ma librairie personnel mais n’importe quel AOP convient.

Placer un label « Vout » sur le fil de sortie afin que la tension Vout soit calculé et accessible facilement dans les différentes courbes de Bode. Le label est accessible par l’icône de droite suivante

3. Choisir « Analyse petits signaux »; 5. Clic; 4. Nombre de points par décade; 5. Fréquence de départ; 6. Fréquence de fin; 1. Clic; 2. Clic pour ajouter un nouveau type de simulation

e) Exploiter les résultats de la simulation

### 2. Lancer la simulation

### 3. La courbe cochée apparait ici en rouge

(Courbe du gain en dB du montage)

### 5. Il est possible de changer la

couleur de la courbe

### 4. Le curseur 1 est ici

sélectionné pour
afficher les valeurs de
la courbe

### 5. Maintien clic gauche sur le triangle

rouge pour déplacer le curseur. Utiliser les fonctions ZOOM si nécessaire

### 6. Affichage des

coordonnées du curseurs


Exploiter la courbe de phase :

### 6. Cocher la courbe de phase

de sortie | 7. Changer la couleur de la courbe

### 8. Utiliser le curseur 2 pour

afficher les coordonnées
du point de mesure

### 9. Maintien clic gauche sur le triangle

vert pour déplacer le curseur. Utiliser les fonctions ZOOM si nécessaire

### 10. Affichage des coordonnées

des curseurs.

## V. Suivi de projet avec GIT sous VSCode

1) Créer le dépôt
Dans GITHUB ou GITLAB

Dans VSCode

### 1. Fermer tous les dossiers

### 2. Cliquer sur

cette icône

Copier l’adresse du dépôt initial

Clic !

### 3. Clic !

### 4. Coller l’adresse

précédemment
copiée dans GITHUB
ou GITLAB

### 5. Entrée

### 6. Choisir le dossier

de dépôt du projet

### 7. Le dépôt est

cloner


2) Installer le viewer Kicode dans VSCode

Il est alors possible de visualiser les schémas et les PCB en cliquant simplement sur les fichiers.

Il est possible d’ouvrir le fichier à partir du menu contextuel (clic droit sur le nom du fichier).

Puis choisir KiCAD Viewer

## VI. PLUGIN

Lancer le gestionnaire de PLUGIN dans le projet

### 1. rentrer le nom du plugin dans

la barre de recherche

### 2. Installer le plugin en cliquant

sur « Installer »

1) Interactive Html BOM
C’est une extension permettant de gérer la BOM avec beaucoup d’option et une interface plus simple.

### 1. Choisir les champs à afficher

### 3. Ne pas oublier le prix

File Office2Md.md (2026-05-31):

# Office2Md

This project intended for parsing and converting Open-XML: 

- DocumentFormat.OpenXml.Packaging.WordprocessingDocument
- DocumentFormat.OpenXml.Packaging.SpreadsheetDocument
- DocumentFormat.OpenXml.Packaging.PresentationDocument

And Pdf files.

to the:

- Markdown documents 
- 11ty-aware documents divided by Headings with build hierarchy automatically (for DocumentFormat.OpenXml.Packaging.WordprocessingDocument)

It means this script **should work with all types of Microsoft Office files** (docx|dotm|dotx xlsx|xlsm|xltx|xltm pptx|pptm|potx|potm|ppsx), but tested only on **.docx**, **.pptx**, **.xlsx**. It works with **.pdf** documents as well.

Conversion based on pure PowerShell code using [Open-XML-SDK](https://github.com/OfficeDev/Open-XML-SDK) ([Nuget package](https://www.nuget.org/packages/DocumentFormat.OpenXml/)) for Office documents. And [iTextSharp](https://www.nuget.org/packages/iTextSharp/) libraries for .pdf. Document conversion make without any additional components/programs like Pandoc for example. No any external API/REST API used. Conversion occurs locally on your computer/VM.

**You can use it for free.**

Office2Md.ps1 provides just a wrapper for classes. You can use classes in the way you want without this wrapper. See **Direct usage of Classes** below.

I'm using [Open-XML-SDK](https://github.com/OfficeDev/Open-XML-SDK) v2.9.1 for this solution and [iTextSharp](https://www.nuget.org/packages/iTextSharp/) v5.5.13.2. But, actually, you don't need to worry about it, because script installs all dependencies itself. In case of any error, you could download those dlls, put them into directory you want and correct path for loading libraries.

## Requirements

Required files:

- Office2Md.ps1
- Office2Md directory with its content:
  - O2mCommon.psm1
  - Office.ps1
  - Pdf.ps1 - *in case you want to convert .pdf documents*
- Office2Md.json

In case you'd like to rename main script `Office2Md.ps1`, you should rename the Directory and .json file according to a new name also.

Log file will have the same name as a main script (Office2Md at the moment) and .log extension. It will be place in the same directory as a main script (Office2Md).

## Assumptions

- Office documents will be represented as hierarchy of PowerShell Classes. It means it can be used in PowerShell 5.0 and above, PowerShell Core.
- Script has been tested on both PowerShell 5.1 & PowerShell Core v6+
- Script was tested on Windows OS only.

## Additionally

In my environment script works in PowerShell Core much faster than on PowerShell 5.1. I don't know why is it, but it is so.

## Features

- Converts **.docx** documents using basic & [Github](https://guides.github.com/features/mastering-markdown/) flawored markdown syntax
  
  - Images
    - in Text
    - in Tables
    - With Links
  - Strings
    - Color (by names & codes: "red", "#aabbcc")
    - Links
    - Bold
    - Italic
    - Underline
    - Strikethrough
    - Highlight
  - Tables
    - with alignment: 
      - right
      - left
      - center
      - none
  - Lists (in text & tables)
    - Ordered (multilevel)
    - Unordered (multilevel)
    - support alpha and roman list item tags. 
    - Unsupported symbols replacement (defined in config file)

- Settings for text color  
  - Color replacement

- Settings for Tables with Merged Cells. Their normalization to the Tables with equivale cells count in each row in order to be available to show as Markdown Table

- Converts **.xlsx** documents using basic & [Github](https://guides.github.com/features/mastering-markdown/) flawored markdown syntax
  
  - Tables with:
    - Automatic detect sheet dimension and delete empty cells from left and top
    - Show **Date** and **Currency** in the settings of culture of the computer you make convertion

- Converts **.pptx** documents using basic & [Github](https://guides.github.com/features/mastering-markdown/) flawored markdown syntax  
  - Titles
  - Text
  - Tables
  - Images (partially)
  
- Converts images from/to 9 format types on the fly. It's widely useful for standardize (reduce) images types to one type in Markdown document. Also some image types could be shown improperly in some software/tools. Supported image types: `bmp`, `gif`, `jpg`, `jpeg`, `ico`, `png`, `tif`, `tiff`, `emf`, `wmf`, `exif`. See **Configurstion** section for details.
- Resize all images in order to standardize their Width or Height by MaxWidth or MaxHeight
- Supports **Plugins** for `ImgItem` class (just for this class yet). See **Plugins** section in this document

- Project has PowerShell script `o2m.ps1` that provides GUI and run `Office2Md.ps1` script under the hood. It work on Windows OS only.

---

So supported **list** items (currently for **.docx** only) are:

- Numbers
- Alpha
- Roman

of any nesting.

---

Examples:

1. Ordered ListItem 1
2. Ordered ListItem 2
   1. Ordered SubItem 1
      a. Alpha SubItem (a)
      b. Alpha subitem (b)
        i. Roman Subitem (i)
        ii. Romain subitem (ii)
- Unordered ListItem 1
- Unordered ListItem 2
  - Unordered subitem 1
  - Unordered subitem 2
    - Unordered sub-subitem 1

---

In OpenXml format list nesting level restricted to: **8**.

## Restrictions

- It is impossible to build a table with merged cells using Markdown syntax. Script analyze table for such things and can automatically normalize it or didn't convert it to markdown one. Instead of conversion, script will put the warning message in red color in the place where table would be. You can drive it by settings in configuration file. See configuration file description.
- Script doesn't work with Shapes, Word Art and anything like that. Only images supported (for **.docx** and **.pptx** files).

## Usage

Office2Md.ps1 script can convert multiple files at once. Also it supports the conversion multiple files into a single Markdown document.

```
.\Office2Md.ps1 [OfficeFilePaths] [OutputDirectory] [-GithubFlawor] [-IntoSingleOne]
```

or

```
.\Office2Md.ps1 -DocPath [OfficeFilePaths] -MdDir [OutputDirectory] [-GithubFlawor] [-IntoSingleOne]
```

- In case of usage without `-IntoSingleOne` option:
  - In [Output Directory] .md file with the same name as each [Office File] will be created and all images will be place into /images directory under the [OutputDirectory].
- In case of usage with `-IntoSingleOne` option:
  - In the [OutputDirectory] will be created a single file with name as first file in [OfficeFilePaths] and all images will be place into /images directory under the [OutputDirectory].

Examples:

```
.\Office2Md.ps1 c:\Documents\1.docx c:\Markdown
```

```
.\Office2Md.ps1 c:\Documents\1.docx,c:\Documents\my.xlsx,c:\Documents\any.pptx,c:\Documents\another.pptx,C:\Pdf\my.pdf c:\Markdown
```

```
.\Office2Md.ps1 c:\Documents\1.docx,c:\Documents\my.xlsx,c:\Documents\any.pptx,c:\Documents\another.pptx,C:\Pdf\my.pdf c:\Markdown -IntoSingleOne
```

## Direct usage of Classes

As I sayed previously, `Office2Md.ps1` just a wrapper for the PowerShell classes, it intended to hide everything from the customer in order to simplify conversion itself. It's ready-to-use solution with command line support for documents conversion.

But if you'd like to include document conversion ability to your own solution, you able to use just Classes.ps1 script that contains a classes for providing conversion. Also you could like to save document data to the disk for future usage (this is much faster than convert document again and again for example). For doing that you might have to know how how it's organized internally a bit.

### Classes hierarchy

Below you can see the classes hierarchy in order to clearly understand how it works.
And... it's pretty simple. :)

```
[BaseItem]
       |
       +------- [DocumentItem]
       |
       +------- [StringItem]
       |
       +------- [ImgItem]
       |
       +------- [ParagraphItem]
       |
       +------- [TableItem]
       |
       +------- [RowItem]
       |
       +------- [CellItem]

[PdfItem]       
```

As I told you ;)

### Call methods

You can use a provided classes in any way you want. In case you'd like' to create your own script using this classes, you must to remember, there are several <u>methods</u> you must to know and use:

| Method | Explanation |
| --- | --- |
| `[DocumentItem]::new($Path, $MdDir, $cfgFile)` | Creates new instance of single .docx, .xlsx or .pptx document. |
| `[PdfItem]::new($Path, $MdDir, $cfgFile)` | Creates new instance of single .pdf document. |
| `[void] ProcessDocument();` | Converts .docx, .xlsx or .pptx document into internal one |
| `[void] CloseDocument();` | Closes a source .docx, .xlsx or .pptx document |
| `[void] SaveToText([string] $FileName)` | Saves .docx, .xlsx or .pptx to the text file. It is a totally silly method and implemented just for fun. |
| `[void] SaveToMarkdown([string] $FileName, [bool] $GithubFlawor)` | Saves .docx, .xlsx or .pptx to markdown format |
| `[void] SaveToMarkdownFor11ty([string] $DirName, [bool] $GithubFlawor)` | Save .docx, .xlsx or .pptx to markdown with splitting the document into Headings with creation hierarchy of documents like Content in Word with 11ty header each |
| `[void] SaveTo([string] $Format, [string] $FileOrDirName, [bool] $GithubFlawor)` | All in one. Saves in the 3 previous ways but the desired type passed in the **Format** variable. Available values are: **Text**, **Markdown**, **11ty** |
| `[string] ToMarkdown()` | Converts processed document to Markdown and returns string contains Markdown document |

$GithubFlawor - if true allows to use those text decorations:

- Strikethrough
- Underline
- Highlight

It is simple to realize additional feature for Githubflawor, but there is no clear comparison them to the **.docx**, **.xlxs** and **.pptx** elements.

If you'd like to use classes without O2mCommon.psm1 module, you must to know that classes use `toLog()` function from O2mCommon.psm1 extensively. You have to define it inside your .ps1 script or module.

Examples of methods usage:

```
$doc = [DocumentItem]::new($DocxPath, $MdDir, $cfgFile)
$doc.ProcessDocument();
$doc.CloseDocument();
$doc.SaveToText((Join-Path $DacDir '1.txt'))
$doc.SaveToMarkdown((Join-Path $DacDir '2.md'))
$doc.SaveToMarkdownFor11ty((Join-Path $DacDir '11ty'), $true)
```

```
$doc = [PdfItem]::new($PdfPath, $MdDir, $cfgFile)
$doc.ProcessDocument();
$doc.CloseDocument();
$doc.SaveToMarkdown((Join-Path $DacDir '2.md'))
```

Object's methods to save to Xml, for example, did not provided because they are don't needed. You can use pure PowerShell commandlets to do save/restore objects.

As you can see, you work just with `[DocumentItem]` or `[PdfItem]` objects. You don't have to know how all of that organized internally and interact between each over. Main methods are the same for `[DocumentItem]` and `[PdfItem]`.

In order to change object's behavior you'd just to inherit the objects and write the code for your needs only.

## Plugins

At the moment, plugins supported just for `[ImgItem]` class. All other classes will be support plugin also soon.
Plugins must be located under `Office2Md\Plugins` folder. Each plugin must have its own folder with unique name. In this folder there must be a `.psm1` module and any count of other files/folders/subfolders.

There are some requirements for the content of `.psm1` module:

- It is required that all functions there, those must be exposed from the module, start with the class name to which they will belong. At the moment: `ImgItem`.
- There are 4 types of plugin functions available for `ImgItem` and all of them are for `ConvertAndSave` method only. Functions names are: 
  - `ImgItem-BeforeConvertAndSave` - calling before any actions in this method. Parameters are:
    - [DocumentFormat.OpenXml.Packaging.ImagePart]$img
    - [System.IO.Stream]$stream
    - [string]$savePath
    - [object]$this.Document.Cfg.Image - points to the configuration part "Image"
  - `ImgItem-ReplaceConvertAndSave` - calling instead of the body of the default method `ConvertAndSave` of `ImgItem` class. But `ImgItem-BeforeConvertAndSave` and `ImgItem-AfterConvertAndSave` will be called if defined. Parameters are:
    - [DocumentFormat.OpenXml.Packaging.ImagePart]$img
    - [System.IO.Stream]$stream
    - [string]$savePath
    - [object]$this.Document.Cfg.Image - points to the configuration part "Image"
  - `ImgItem-ResizeImage` - calling instead of default resize code inside `ConvertAndSave` method of the `ImgItem` class. Won't be called if you defined `ImgItem-ReplaceConvertAndSave` because `ImgItem-ReplaceConvertAndSave` overload this code. Parameters are:
    - [System.IO.Stream]$stream
    - [object]$this.Document.Cfg.Image - points to the configuration part "Image"
  - `ImgItem-AfterConvertAndSave` - calling after any actions in this method. Parameters are:
    - [DocumentFormat.OpenXml.Packaging.ImagePart]$img
    - [System.IO.Stream]$stream
    - [string]$savePath
    - [object]$this.Document.Cfg.Image - points to the configuration part "Image"

You are not obliged to define all of the functions above. Just those you want to.

See `Office2Md\Plugins\ImageResize` for example.

## Configuration file description

| Key | Subkey | SubSubkey | Type | Available values | Examples | Meaning |
| --- | --- | --- | --- | --- | --- | --- |
| Toc | | | Object | | | Styles those will be considered as **Table of Content** |
| | TocHeading | | Array of strings | Any strings | \["tocH1", "tocH2", "tocH3"\] | Don't using at the moment |
| | Toc1 | | Array of strings | Any strings | \["toc1", "toc2", "toc3"\] | Don't using at the moment |
| | Toc2 | | Array of strings | Any strings | \["toc1", "toc2", "toc3"\] | Don't using at the moment |
| | Toc3 | | Array of strings | Any strings | \["toc1", "toc2", "toc3"\] | Don't using at the moment |
| | Toc4 | | Array of strings | Any strings | \["toc1", "toc2", "toc3"\] | Don't using at the moment |
| Head | | | Object | | | Styles those will be considered as **Headings** |
| | Head1 | | Array of strings | Any strings | \["head1", "otherHead", "overhead"\] | |
| | Head2 | | Array of strings | Any strings | \["head1", "otherHead", "overhead"\] | |
| | Head3 | | Array of strings | Any strings | \["head1", "otherHead", "overhead"\] | |
| | Head4 | | Array of strings | Any strings | \["head1", "otherHead", "overhead"\] | |
| | Head5 | | Array of strings | Any strings | \["head1", "otherHead", "overhead"\] | |
| | Head6 | | Array of strings | Any strings | \["head1", "otherHead", "overhead"\] | |
| List | | | Array of strings | Any strings | \["ListParagraph", "Bullet1", null\] | Styles those will be considered as **Lists** |
| Common | | | Array of strings | Any strings | \["Normal", "Caption", "Hyperlynk", null\] | Styles those will be considered as **Common Text** or **Links** |
| Image | | | | | | Options for working with Images |
| | Prefix | | String | Any strings | | Prefix for every image that will be put before /images/ImageName\.ext\. Very useful for creating content for 11ty for example |
| | UsePrefix | | Boolean | true, false | | Use the prefix above or not |
| | Embed | | Boolean | true, false | | Embed images directly to the Markdown document in order to have a single document without links to the images it contains |
| | Convert | | Object | | | Allow to convert images from one format to another |
| | | UseConversion | Boolean | | | If **true**, then script will try to convert all images according Replace rules\. If there is no such extension defined in rules, then image will be saved as\-is with its default extension |
| | | Replace | Array of objects | | | Contains simple from \- to pairs\. And allows to convert images with extension "From" to type with extension "To"\. Example: \`"Replace" : \[\{"From" : "\.emf", "To" : "\.jpg"\},<br><br>\{"From" : "\.wmf", "To" : "\.jpg"\}\]\`\. You can use the next extensions: \`bmp\`, \`gif\`, \`jpg\`,\` jpeg\`, \`ico\`, \`png\`, \`tif\`, \`tiff\`, \`emf\`, \`wmf\`, \`exif\` with or without leading "\."\. All others will be ignored\. |
| | | Resize | | Object | | Allows to resize images in order to make them the same by Width or Height |
| | | | UseResize | Boolean | | If **True** all images will be resized according to the rules |
| | | | MaxWidth | Unsigned int | | If above the 0, then Width of all images will be resized to this value\. **MaxWith** have apriority on **MaxHeight**\. |
| | | | MaxHeight | Unsigned int | | If above the 0, then Height of all images will be resized to this value\. **MaxWith** have apriority on **MaxHeight**\. |
| | | | DoNotResizeLessThanMax | Boolean | | If **true**, then all images those have Width or Height less than MaxHeight or MaxWidth won't be resized |
| | | | InterpolationMode | String | | Resize algorythm\. Can be one of:**HighQualityBicubicorHighQualityBilinear** |
| ReplaceThis | | | Array of objects | | | |
| | From | | String | Any string \(including Unicode strings or their definition for PowerShell\) | Kb\. | \{"From" : "Kb\.", "To" : "Kilobytes"\} |
| | To | | String | Any string | Kilobytes | \{"From" : "\u2122", "To" : "&trade;"\} |
| Table | | | | | | Options for working with tables |
| | Standardize | | Boolean | true, false | | If true, checks and makes \(if required\) tables with different cells count in rows to the same count in row\. It is required for table can be represented as Markdown |
| Colors | | | | | | Options for working with colors of text |
| | UseColors | | Boolean | true, false | | Use ability to color the text or left it uncolored |
| | Replace | | Object | | \{"From" : "\#FFFFFF", "To" : "\#000000"\} | Replaces one color definition to another one\. Useful when color of text set as **white** or **\#FFFFFF** |
| | | From | String | Any string representing a color \(their name or RGB\) | \{"From" : "\#FFFFFF", "To" : "\#000000"\} | |
| | | To | String | Any string representing a color \(their name or RGB\) | \{"From" : "white", "To" : "black"\} | |
| Workbook | | | Object | | | Options available for the Excel Workbooks \(\.xlsx files\) |
| | SheetHeading | | Object | | | Object for combining purposes related to the Tab names definition |
| | | UseTabName | Boolean | true, false | | Use the tab name as a prefix for the tab content or not |
| | | Template | String | Any string\. Use special placeholder \{TabName\}\. It will be replaced by the name of a current Tab | "\#\#\# \{TabName\}" | Will be used if **UseTabName** is set to **true** |
| Pdf | | | Object | | | Options we have to convert the PDF documents |
| | UsePageNumbers | | Boolean | true, false | | Put the page number to the resulting Markdown |
| | Position | | string | "header" or "footer" | "footer" | Case insensitive |
| | Template | | | Any string\. Use special placeholder \{PageNumber\}\. It will be replaced by the number of a current page | "\#\#\#\# \{PageNumber\}" | Will be used if **UsePageNumber** is set to **true** |

## Known bugs/flaws/issues

- Complex/Distributed Lists could be shown improperly (I don't know how to separate one list to another one using OpenDoc format. Algorithm I've implemented is not work properly in some cases)
- Table of Content didn't implemented
- For **.pptx**, **.xlsx** and **.pdf** files didn't implemented any styles, colors etc, I mean there is no any decoration for those types of files
- On some environments (depends on Windows and/or PowerShell configuration) `Office2Md.ps1` script can't automatically download and install required packages [OpenXml](https://www.nuget.org/packages/DocumentFormat.OpenXml/) and [iTextSharp](https://www.nuget.org/packages/iTextSharp/). In this case You can do it manually by choosing one of two ways below:
  - Install them by [Install-Package](https://docs.microsoft.com/en-us/powershell/module/packagemanagement/install-package?view=powershell-7.1) CommandLet. For example:
    - `Install-Package iTextSharp -MinimumVersion 5.5.13.2`
    - `Install-Package DocumentFormat.OpenXml -MinimumVersion 2.9.1`
  - Download `.nuget` packages from the URLs above and unzip them into: `C:\Users\<LoginName>\AppData\Local\PackageManagement\Nuget\Packages` to the personal folder for each. For example into: `C:\Users\<LoginName>\AppData\Local\PackageManagement\NuGet\Packages\iTextSharp.5.5.13.2` and `C:\Users\<LoginName>\AppData\Local\PackageManagement\NuGet\Packages\Open-XML-SDK.2.9.1`

## ToDo

- Pipeline (Best Practices compliance, Digital signature, Tests)
- Versioning
- Releases
- Decorations for **.pptx**, **.xlsx** and **.pdf** files
- ...

## Author

Contact: 

- Email: [Alexander Ivanov](mailto:Alexander.Ivan0v@outlook.com)
- Skype **VeryComplexName**

## Example

In the directory **TestOffice** in the repository you can find a **Text.docx**, **Test1.pptx**, **Test2.xlsx** and **Test3.pdf** documents with a different styles, list, tables and they overlapping.
Below you can see the conversion result (you could compare result with original **Text.docx**, **Test1.pptx**, **Test2.xlsx** and **Test3.pdf** in the repository). Gitlab doesn't support many of extended features, but you could try to see it in Markdown editors/viewers ([Mark Text](https://marktext.app/)) for example or using Github or in an amount of plugins for Web browsers.
In **TestOffice** directory you can also find the resultant document **Test.md**.

Below the convertion result of 3 Office documents **Text.docx**, **Test1.pptx**, **Test2.xlsx** and **Test3.pdf** for conversion `-IntoSingleOne` option has been used. So, all of mentioned files were merged into a single one in order they are provided in the command line for script. Command for get this result you can find in `TestOffice/IntoSingle.cmd`

Below you can see how it looks in Gitlab. *Remember: Gitlab doesn't use a full power of Markdown documents. Use separate programs or browser plugins for see all the things available*. You can see resultant file **Test.md** in the **TestOffice** folder also.

---

This is simple string

LogoDescription automatically generated

This is complex string with **Bold text**, *Italic text*, ***Bold and Italic text***, ~~Strike through text~~, <u>Underline text</u> and <span style="color:#FF0000">Colored text</span>\.

<u>Below is Unordered list</u> <u>\(and this line is underscored\)</u><u>:</u>

- **Bold** and ~~Strikethrough~~ text
- *Italic* <span style="color:#538135">Colored</span> and <u>*Underline*</u> <u>*Italic*</u>
  - <span style="color:#C45911">**Different color and Bold**</span>

<u>Below</u> <u>O</u><u>rdered list \(and this line is underscored\)</u><u>:</u>

1. <span style="color:#FF0000">**Bold Red**</span>
2. ~~*Italic and Strikethrough*~~
   b. Simple text

<u>Below ordered list tagged by Roman symbols \(and this line is underscored\):</u>

i. Roman1
ii. <span style="color:#00B050">Roman2 Colored</span>

<u>Below ordered list tagged by Alpha symbols \(and this line is underscored\):</u>

b. <span style="color:#C00000">*Alpha Colored and Italic*</span>
c. Alpha2 Common

| Left aligned column | Centered column | Right aligned column |
| --- |:---:| ---:|
| <br>- <span style="color:#2F5496">Colored</span><br>- <span style="color:#2F5496">*Same color and Italic*</span><br>- Common **Bold** <span style="color:#BF8F00">Different color</span> | **Bold** | 77676767 |
| <u>~~***Bold Italic Underline***~~</u> | <mark>Common</mark> <mark>Highlighted</mark>below you can see the image with link | <br>1. Common<br>2. <span style="color:#C9C9C9">*Grayed text*</span><br>3. ***Italic*** |
| ShapeDescription automatically generated with low confidence | IconDescription automatically generated (https://guides.github.com/features/mastering-markdown/) | IconDescription automatically generated |

-----

This is a title

| 1 | 2 | 3 |
| --- | ---- | --- |
| dfd | dfdf | dfd |
| dfd | dfd  | dfd |

| www | eee | rrr | ttt |
| --- | --- | --- | --- |
| | | | |

Textbox



IconDescription automatically generated

Second slide title

| Title Left aligned | Title Center aligned | Title Right Aligned |
| --- | --- | --- |
| qqq | rrrrrrr | 66666666666 |
| W w w wwww www<br><br>Dfdf d fddf dfd<br><br>Dfdf df dfd<br><br>Gfgfgfgfgf<br><br>fgfgfgfgfgf | rrrrrrrrrrrrrrrrr | Ggggg<br><br>Gfgfgffgfg<br><br>fgfhvnghjhjggggh |



-----

### Sheet3

| | | | 1 | 2 | 3 | 4 | 5 |
| ---- | --- | --- | --- | --- | --- | --- | --- |
| | | | 6 | 7 | 8 | 9 | 10  |
| | | | 11  | 12  | 13  | 14  | 15  |
| | | | | | | | |
| 4,35 | | | | | | | |
| | | | | | | | |
| | www | | | | | | |
| | | | | | | | |
| | | | | | | | |
| | 22\.11\.2021 | | | | | | |

### Sheet2

| 22  | | |
| --- | --- | ----- |
| | 22\.11\.2021 | |
| | | 44\.6 |

### Sheet1

| 12\.11\.2021 | 2 | 3 |
| --- | --- | --- |
| 4,00 | FALSE | 6 |
| 789\.6789 | 394\.83945 | 9 |

-----

Using the LIFEBOOK Application Panel
Launching Applications with the LIFEBOOK Application Panel
The application panel enables you to launch applications with the touch of a button when your system is on. Pressing 
any of the buttons will launch a user-defined application. Your notebook is pre-installed with software utilities that 
let you operate and configure your LIFEBOOK Application Panel.
Configuring your LIFEBOOK Application Panel  
When you start Windows, the LIFEBOOK Application Panel is automatically activated. As an application launcher, the 
LIFEBOOK Application Panel is very flexible, giving you a variety of options. To set up the panel to best suit your needs, 
we have provided the Application Panel Setup utility that quickly and easily helps you make the most of this valuable 
feature.
To configure your LIFEBOOK Application Panel with Application Panel Setup:  
1 Right-click on the Start icon. Click All Apps.
2 Click on Setup of LIFEBOOK Application Panel. The Button Setting utility will appear. The tabs that appear in the 
utility window correspond to the application buttons on the LIFEBOOK Application Panel. When you receive your 
notebook, these buttons are pre-configured to launch specific programs.
To change an application associated with the Application buttons:  
1 Click on the tab for the button you would like to reconfigure – for example, Application A. 
2 Click on the Enable this button check box if it is unchecked, then click on the [Application Registration] button. 
3 Click the Start Program check box, then click [Next]
4 On the screen that appears, click Select from Apps and scroll through the list to select the application you want 
to start with the Application A button.
5 Click [Next] -> [Next] -> [Finish]. On the Button Setting window, click [Apply], then click [OK]. The button will now 
launch the new application.
1 - 

#### 1

The Internet tab is a little bit different. It comes set to launch your default Internet browser (Internet Explorer), unless 
you have changed it in Windows. To reconfigure it to launch another program, follow these steps:
1 Click on the Internet tab. 
2 Click on the Enable this button check box if it is unchecked, then click on the [Application Registration] button. 
3 Click the Start program check box, then click [Next].
4 On the screen that appears, click the Select from Apps check box and scroll through the list to select the 
application you want to start with the Internet button.
5 Click [Next] -> [Next] -> [Finish]. On the Button Setting window, click [Apply], then click [OK]. 
The button will now launch the new application. If you want to return to launching your Windows default Internet 
browser with this button, click on the Start Browser check box instead of the Start program check box. Be aware that 
you will erase the settings for the “other application”. If you wish to go back to launching the “other application” from 
this button, you will need to reconfigure it as described above.
When you have finished with button settings, click [OK], and the new settings will take effect. You can reconfigure 
your LIFEBOOK Application Panel as often as you like. 
IF ONE OF THE APPLICATION LAUNCHER BUTTONS IS IDENTIFIED AS AN INTERNET LAUNCHER, THE BUTTON CAN STILL BE CONFIGURED TO LAUNCH 
ANY APPLICATION YOU WISH; IT IS NOT LIMITED TO BEING AN INTERNET BROWSER.
2 - 

#### 2

-----

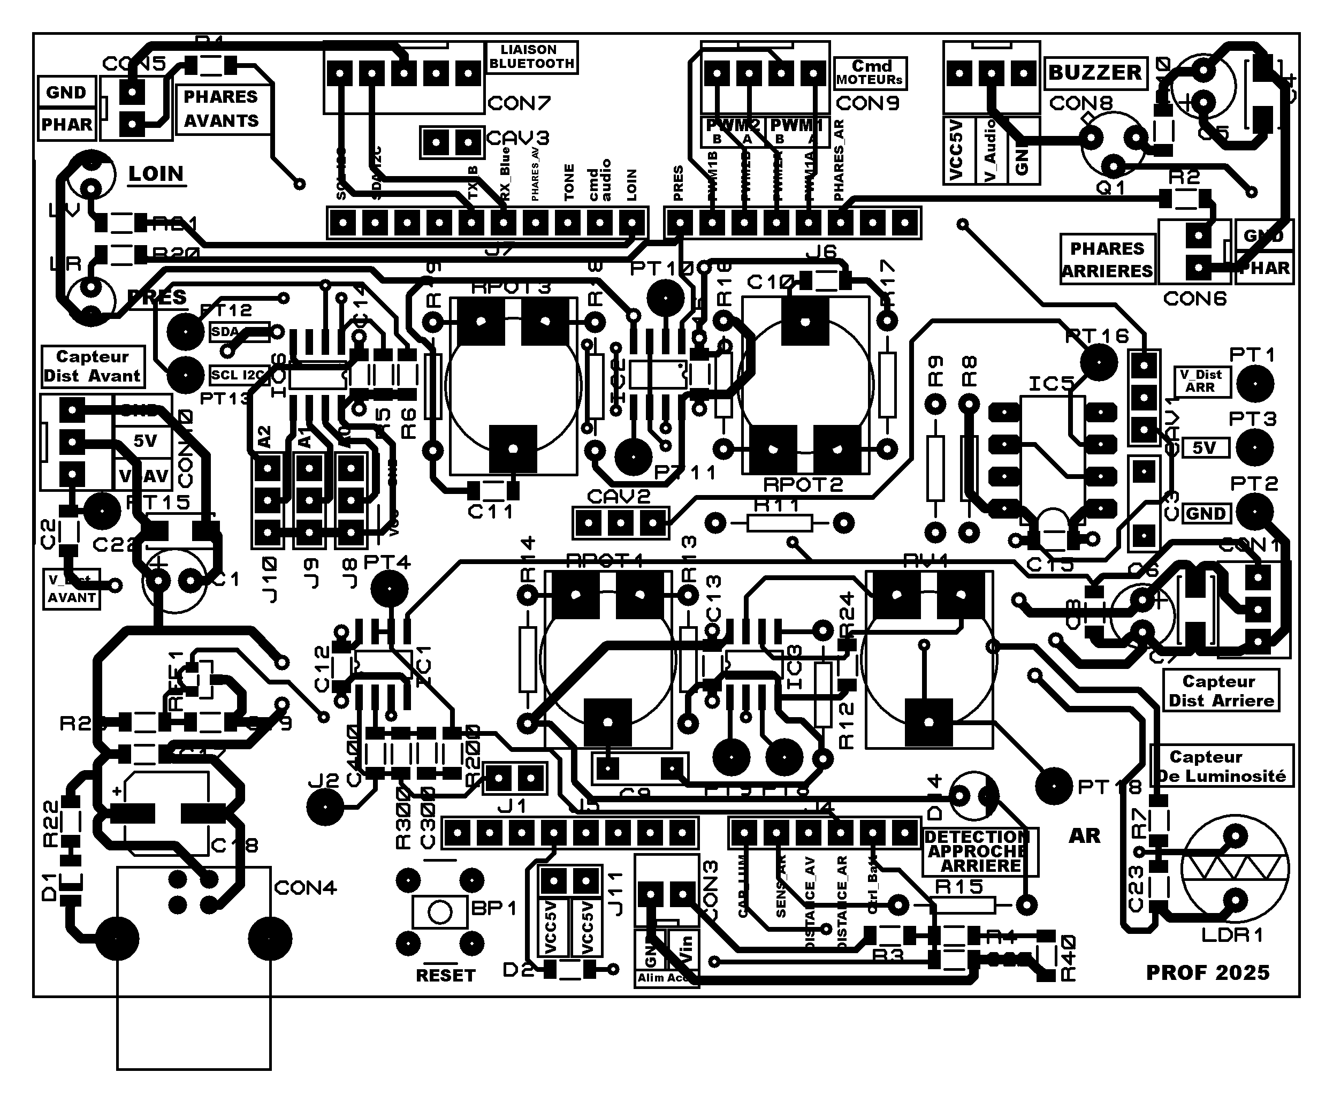
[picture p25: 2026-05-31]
hardware/carte prof (1).bmp

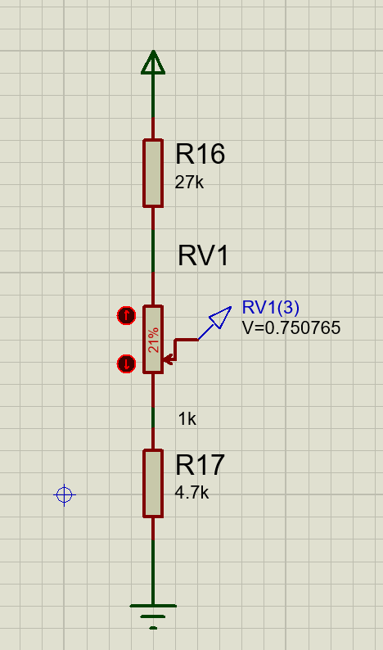
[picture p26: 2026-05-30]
hardware/proteus/Simu de RPOT2.png

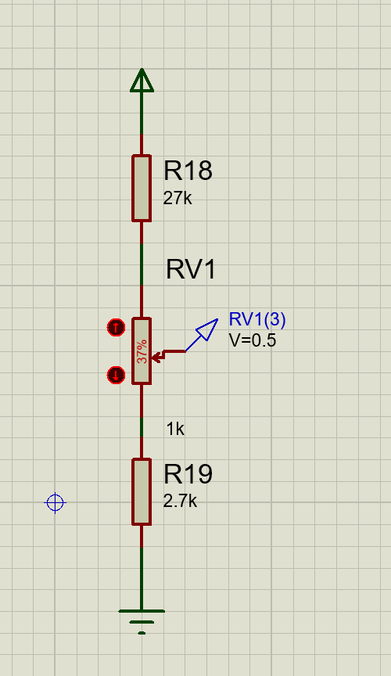
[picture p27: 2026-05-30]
hardware/proteus/Simu RPOT3.png

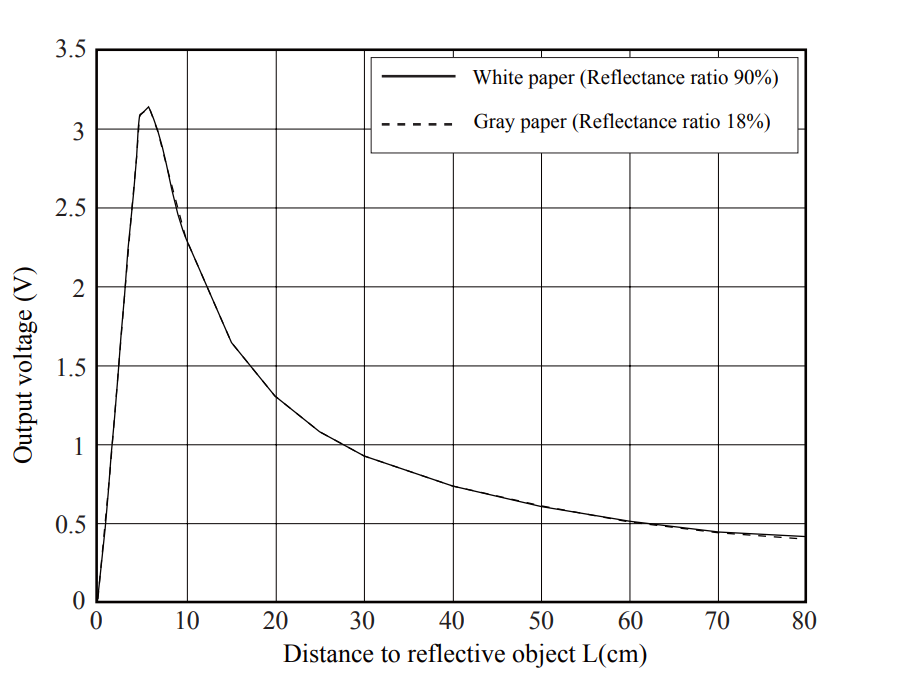
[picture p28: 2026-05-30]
docs/FICHE DOCUMENTATION radar de recul avec tension Loin et Près.png

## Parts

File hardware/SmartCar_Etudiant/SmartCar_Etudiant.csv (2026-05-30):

Reference | Qty | Value | DNP | Exclude from BOM | Exclude from Board | Footprint | Datasheet
BP1 | 1 | Button_Reset |  |  |  | My_footprints:Button_Reset | https://www.farnell.com/datasheets/3975354.pdf
C1,C6 | 2 | 10uF |  |  |  | Capacitor_SMD:C_1206_3216Metric | https://4donline.ihs.com/images/VipMasterIC/IC/SEMS/SEMS-S-A0008384515/SEMS-S-A0008888671-1.pdf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
C2,C5,C8,C9,C10,C11,C12,C13,C14,C15,C16,C17,C19,C20,C23 | 15 | 100n |  |  |  | Capacitor_SMD:C_1206_3216Metric | https://content.kemet.com/datasheets/KEM_C1002_X7R_SMD.pdf
C3 | 1 | 100n |  |  |  | My_footprints:CAPA_FILM_L7.2mm_W2.5mm_P5.00mm | https://content.kemet.com/datasheets/KEM_F3101_R82.pdf
C4 | 1 | 22uF |  |  |  | Capacitor_SMD:C_1206_3216Metric | https://4donline.ihs.com/images/VipMasterIC/IC/SEMS/SEMS-S-A0008384515/SEMS-S-A0008888671-1.pdf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
C18 | 1 | 47uF |  |  |  | My_footprints:CAP ELECTROLY CMS 5MM | https://www.farnell.com/datasheets/3486024.pdf
C21,C30 | 2 | ~ |  |  |  | Capacitor_SMD:C_1206_3216Metric | https://content.kemet.com/datasheets/KEM_C1002_X7R_SMD.pdf
CON1,CON8,CON10 | 3 | Conn_01x03 |  |  |  | Connector_Molex:Molex_KK-254_AE-6410-03A_1x03_P2.54mm_Vertical | https://www.gotronic.fr/pj-1261.pdf
CON3,CON5,CON6 | 3 | Conn_01x02 |  |  |  | Connector_Molex:Molex_KK-254_AE-6410-02A_1x02_P2.54mm_Vertical | https://www.gotronic.fr/pj-1261.pdf
CON7 | 1 | Conn_01x05 |  |  |  | Connector_Molex:Molex_KK-254_AE-6410-05A_1x05_P2.54mm_Vertical | https://www.gotronic.fr/pj-1261.pdf
CON9 | 1 | Conn_01x04 |  |  |  | Connector_Molex:Molex_KK-254_AE-6410-04A_1x04_P2.54mm_Vertical | https://www.gotronic.fr/pj-1261.pdf
CONN2 | 1 | USB_B |  |  |  | My_footprints:USB_B | https://4donline.ihs.com/images/VipMasterIC/IC/SCMP/SCMP-S-A0010725696/SCMP-S-A0010725696-1.pdf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
D2,D3 | 2 | BAT42W-V |  |  |  | My_footprints:D_SOD-123 | https://www.farnell.com/datasheets/3775987.pdf
J4 | 1 | Conn_Sil_06 |  |  |  | Connector_PinHeader_2.54mm:PinHeader_1x06_P2.54mm_Vertical | https://www.farnell.com/datasheets/2905949.pdf 0 0 Centrer Centrer 0 0
J5,J6 | 2 | Conn_Sil_08 |  |  |  | Connector_PinHeader_2.54mm:PinHeader_1x08_P2.54mm_Vertical | https://www.farnell.com/datasheets/2905949.pdf 0 0 Centrer Centrer 0 0
J7 | 1 | Conn_Sil_10 |  |  |  | Connector_PinHeader_2.54mm:PinHeader_1x10_P2.54mm_Vertical | https://www.farnell.com/datasheets/2905949.pdf 0 0 Centrer Centrer 0 0
JP1,JP2 | 2 | Jumper_3_Bridged12 |  | Exclure de la Liste du Matériel |  | Connector_PinHeader_2.54mm:PinHeader_1x03_P2.54mm_Vertical | https://www.farnell.com/datasheets/2905949.pdf
JP3 | 1 | Jumper_2 |  |  |  | Connector_PinHeader_2.54mm:PinHeader_1x02_P2.54mm_Vertical | https://www.farnell.com/datasheets/2905949.pdf
JP4,JP5,JP6 | 3 | Jumper_3 |  | Exclure de la Liste du Matériel |  | Connector_PinHeader_2.54mm:PinHeader_1x03_P2.54mm_Vertical | https://www.farnell.com/datasheets/2905949.pdf
LDR1 | 1 | LDR |  |  |  | My_footprints:LDR_11x9.4mm_4.1x3.4mm_Vertical | https://www.farnell.com/datasheets/77395.pdf
LED1 | 1 | LED_BLEU |  |  |  | LED_SMD:LED_1206_3216Metric | https://www.farnell.com/datasheets/2045849.pdf
LED2 | 1 | LED Orange |  |  |  | My_footprints:LED_D3.0mm_Orange | https://www.farnell.com/datasheets/1747868.pdf
LED3 | 1 | LED Rouge |  |  |  | LED_THT:LED_D3.0mm | https://www.farnell.com/datasheets/67052.pdf
LED4 | 1 | LED Verte |  |  |  | My_footprints:LED_D3.0mm_Green | https://www.farnell.com/datasheets/67043.pdf
Q2 | 1 | 2N2222A |  |  |  | My_footprints:TO-18 | https://www.farnell.com/datasheets/2861172.pdf
R1,R2 | 2 | 220 |  |  |  | Resistor_SMD:R_1206_3216Metric_Pad1.30x1.75mm_HandSolder | ~
R3 | 1 | 5.6k |  |  |  | Resistor_SMD:R_1206_3216Metric_Pad1.30x1.75mm_HandSolder | ~
R4 | 1 | 3.3k |  |  |  | Resistor_SMD:R_1206_3216Metric_Pad1.30x1.75mm_HandSolder | ~
R5,R6 | 2 | 10k |  |  |  | Resistor_SMD:R_1206_3216Metric_Pad1.30x1.75mm_HandSolder | ~
R7 | 1 | 22k |  |  |  | Resistor_SMD:R_1206_3216Metric_Pad1.30x1.75mm_HandSolder | ~
R8,R17,R19 | 3 | 470 |  |  |  | Resistor_THT:R_Axial_DIN0204_L3.6mm_D1.6mm_P7.62mm_Horizontal | ~
R9 | 1 | 2.2k |  |  |  | Resistor_THT:R_Axial_DIN0204_L3.6mm_D1.6mm_P7.62mm_Horizontal | ~
R10 | 1 | 1M |  |  |  | Resistor_SMD:R_1206_3216Metric_Pad1.30x1.75mm_HandSolder | ~
R11 | 1 | 10k |  |  |  | Resistor_THT:R_Axial_DIN0204_L3.6mm_D1.6mm_P7.62mm_Horizontal | ~
R12,R13,R14,R15 | 4 | 1k |  |  |  | Resistor_THT:R_Axial_DIN0204_L3.6mm_D1.6mm_P7.62mm_Horizontal | ~
R16,R18 | 2 | 5.6k |  |  |  | Resistor_THT:R_Axial_DIN0204_L3.6mm_D1.6mm_P7.62mm_Horizontal | ~
R20,R21,R23 | 3 | 680 |  |  |  | Resistor_SMD:R_1206_3216Metric_Pad1.30x1.75mm_HandSolder | ~
R22 | 1 | 1k |  |  |  | Resistor_SMD:R_1206_3216Metric_Pad1.30x1.75mm_HandSolder | ~
R24 | 1 | 2.2k |  |  |  | Resistor_SMD:R_1206_3216Metric_Pad1.30x1.75mm_HandSolder | ~
R25,R30,R40 | 3 | ~ |  |  |  | Resistor_SMD:R_1206_3216Metric_Pad1.30x1.75mm_HandSolder | ~
REF1 | 1 | ZTL431 |  |  |  | My_footprints:SOT-23 | https://www.farnell.com/datasheets/2096831.pdf
RPOT1 | 1 | 470 |  |  |  | My_footprints:Potentiometer standard | https://www.farnell.com/datasheets/2661581.pdf
RPOT2,RPOT3 | 2 | 1k |  |  |  | My_footprints:Potentiometer standard | https://www.farnell.com/datasheets/2661581.pdf
RV1 | 1 | 47k |  |  |  | My_footprints:Potentiometer standard | https://www.farnell.com/datasheets/2661581.pdf
TP1,TP2,TP3,TP4,TP5,TP6,TP7,TP9,TP12,TP13,TP16,TP18 | 12 | TestPoint |  |  |  | My_footprints:PT | https://www.gotronic.fr/art-50-cosses-poignard-coy71-4692.htm
U1,U2,U3 | 3 | MCP6002 |  |  |  | My_footprints:SO8_3.9x4.9mm_P1.27mm | https://www.microchip.com/en-us/product/mcp6002
U4 | 1 | MCP9801_SO8,NE555D |  |  |  | My_footprints:DIL8,U5 | http://ww1.microchip.com/downloads/en/DeviceDoc/21909d.pdf,http://www.ti.com/lit/ds/symlink/ne555.pdf

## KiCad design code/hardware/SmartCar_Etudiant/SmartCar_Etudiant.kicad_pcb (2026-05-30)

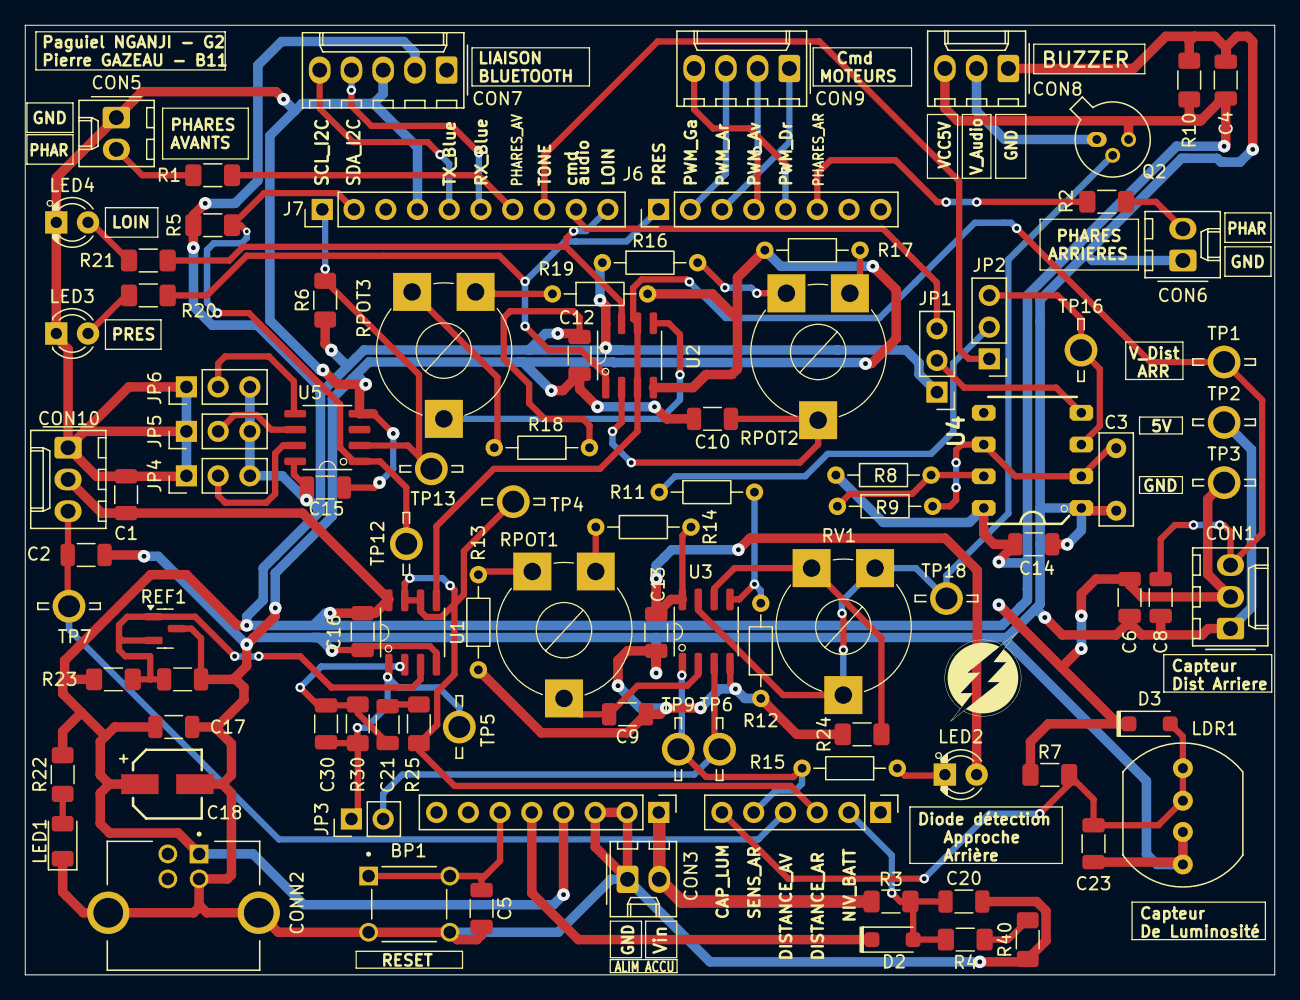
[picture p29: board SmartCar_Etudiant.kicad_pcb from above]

Board: 2 copper layers, 100.0 x 76.0 mm, 98 parts (0 on the bottom side), 58 nets.

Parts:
BP1: SW_TS02-66-60-BK-260-LCR-D; Button_Reset
C1, C6: 10uF; C_1206_3216Metric
C2, C5, C8, C9, C10, C12, C13, C14, C15, C16, C17, C19, C20, C23: 100n; C_1206_3216Metric
C3: 100n; CAPA_FILM_L7.2mm_W2.5mm_P5.00mm
C4: 22uF; C_1206_3216Metric
C18: 47uF; CAP ELECTROLY CMS 5MM
C21, C30: C_1206_3216Metric
CON1, CON8, CON10: Conn_01x03; Molex_KK-254_AE-6410-03A_1x03_P2.54mm_Vertical
CON3, CON5, CON6: Conn_01x02; Molex_KK-254_AE-6410-02A_1x02_P2.54mm_Vertical
CON7: Conn_01x05; Molex_KK-254_AE-6410-05A_1x05_P2.54mm_Vertical
CON9: Conn_01x04; Molex_KK-254_AE-6410-04A_1x04_P2.54mm_Vertical
CONN2: USB_B
D2, D3: BAT42W-V; D_SOD-123
J4: Conn_Sil_06; PinHeader_1x06_P2.54mm_Vertical
J5, J6: Conn_Sil_08; PinHeader_1x08_P2.54mm_Vertical
J7: Conn_Sil_10; PinHeader_1x10_P2.54mm_Vertical
JP1, JP2: Jumper_3_Bridged12; PinHeader_1x03_P2.54mm_Vertical
JP3: Jumper_2; PinHeader_1x02_P2.54mm_Vertical
JP4, JP5, JP6: Jumper_3; PinHeader_1x03_P2.54mm_Vertical
LDR1: LDR; LDR_11x9.4mm_4.1x3.4mm_Vertical
LED1: LED_BLEU; LED_1206_3216Metric
LED2: LED Orange; LED_D3.0mm_Orange
LED3: LED Rouge; LED_D3.0mm
LED4: LED Verte; LED_D3.0mm_Green
Q2: 2N2222A; TO-18
R1, R2: 220; R_1206_3216Metric_Pad1.30x1.75mm_HandSolder
R3: 5.6k; R_1206_3216Metric_Pad1.30x1.75mm_HandSolder
R4: 3.3k; R_1206_3216Metric_Pad1.30x1.75mm_HandSolder
R5, R6: 10k; R_1206_3216Metric_Pad1.30x1.75mm_HandSolder
R7: 22k; R_1206_3216Metric_Pad1.30x1.75mm_HandSolder
R8, R17, R19: 470; R_Axial_DIN0204_L3.6mm_D1.6mm_P7.62mm_Horizontal
R9: 2.2k; R_Axial_DIN0204_L3.6mm_D1.6mm_P7.62mm_Horizontal
R10: 1M; R_1206_3216Metric_Pad1.30x1.75mm_HandSolder
R11: 10k; R_Axial_DIN0204_L3.6mm_D1.6mm_P7.62mm_Horizontal
R12, R13, R14, R15: 1k; R_Axial_DIN0204_L3.6mm_D1.6mm_P7.62mm_Horizontal
R16, R18: 5.6k; R_Axial_DIN0204_L3.6mm_D1.6mm_P7.62mm_Horizontal
R20, R21, R23: 680; R_1206_3216Metric_Pad1.30x1.75mm_HandSolder
R22: 1k; R_1206_3216Metric_Pad1.30x1.75mm_HandSolder
R24: 2.2k; R_1206_3216Metric_Pad1.30x1.75mm_HandSolder
R25, R30, R40: R_1206_3216Metric_Pad1.30x1.75mm_HandSolder
REF1: ZTL431; SOT-23
RPOT1: 470; Potentiometer standard
RPOT2, RPOT3: 1k; Potentiometer standard
RV1: 47k; Potentiometer standard
TP1, TP2, TP3, TP4, TP5, TP6, TP7, TP9, TP12, TP13, TP16, TP18: TestPoint; PT
U1, U2, U3: MCP6002; SO8_3.9x4.9mm_P1.27mm
U4: NE555D; DIL8
U5: MCP9801_SO8; SO8_3.9x4.9mm_P1.27mm

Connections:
+2V5: C19.1, R23.1, REF1.2 (REF), REF1.3 (K), U1.3
+3.3V: D2.1 (K), J5.5
+5V: C1.2, C4.1, C6.2, C12.1, C13.1, C14.1, C15.1, C16.1, C17.1, C18.1, CON1.2, CON7.2, CON8.3, CON10.2, CONN2.1 (VBUS), D3.1 (K), J5.4, JP1.1 (A), JP4.3 (B), JP5.3 (B), JP6.3 (B), LED2.2 (A), Q2.3 (C1), R5.1, R6.1, R7.1, R8.1, R10.2, R14.2, R16.1, R18.1, R22.2, R23.2, TP3.1 (TP), U1.8, U2.8, U3.8, U4.8 (VCC), U5.8 (V_{DD})
CAP_LUM: C23.1, D3.2 (A), J4.6, LDR1.1, R7.2
CMD_GENE_AUDIO: J7.9, JP1.3 (B)
DISTANCE_AR: J4.3, R25.1, TP4.1 (TP), U1.6, U1.7
DISTANCE_AV: C2.1, CON10.3, J4.4, TP7.1 (TP)
GND: BP1.3, BP1.4, C1.1, C2.2, C3.2, C4.2, C5.2, C6.1, C8.2, C9.2, C10.2, C12.2, C13.2, C14.2, C15.2, C16.2, C17.2, C18.2, C19.2, C20.2, C23.2, CON1.1, CON3.1, CON5.1, CON6.1, CON7.3, CON8.1, CON10.1, CONN2.4 (GND), CONN2.5 (Shield), J5.2, J5.3, J7.4, JP4.1 (A), JP5.1 (A), JP6.1 (A), LDR1.2, LED1.1 (K), LED3.1 (K), LED4.1 (K), R10.1, R12.1, R13.1, R17.2, R19.2, R24.1, R40.1, REF1.1 (A), TP2.1 (TP), U1.4, U2.4, U3.4, U4.1 (GND), U5.4 (GND)
LOIN: J7.10, R21.2, U2.7
NIV_BATT: C20.1, D2.2 (A), J4.2, R3.1, R4.2
unnamed: C9.1, RPOT1.2, U3.2
unnamed: C10.1, RPOT2.2, U2.2
unnamed: RPOT3.2, U2.5
unnamed: C21.1, R25.2
unnamed: C21.2, C30.1, R30.1, U1.2
unnamed: C8.1, CON1.3, TP1.1 (TP), U1.5, U2.3, U2.6
unnamed: CON5.2, R1.1
unnamed: CON6.2, R2.1
unnamed: JP1.2 (C), U4.4 (R)
unnamed: JP2.3 (B), TP16.1 (TP), U4.3 (Q)
unnamed: JP2.2 (C), R11.1
unnamed: C30.2, JP3.1 (A), R30.2, TP5.1 (TP), U1.1
unnamed: JP3.2 (B), TP6.1 (TP), U3.3
unnamed: JP4.2 (C), U5.7 (A0)
unnamed: JP5.2 (C), U5.6 (A1)
unnamed: JP6.2 (C), U5.5 (A2)
unnamed: LED1.2 (A), R22.1
unnamed: LED2.1 (K), R15.1
unnamed: LED3.2 (A), R20.1
unnamed: LED4.2 (A), R21.1
unnamed: Q2.2 (B1), RV1.2, RV1.3, TP18.1 (TP), U3.7
unnamed: R4.1, R40.2
unnamed: R11.2, R12.2, U3.5
unnamed: R13.2, RPOT1.1
unnamed: R14.1, RPOT1.3
unnamed: R16.2, RPOT2.1
unnamed: R17.1, RPOT2.3
unnamed: R18.2, RPOT3.1
unnamed: R19.1, RPOT3.3
unnamed: R24.2, RV1.1, U3.6
unnamed: R8.2, R9.1, U4.7 (DIS)
unnamed: C3.1, R9.2, U4.2 (TR), U4.6 (THR)
PHARES_AR: J6.6, R2.2
PHARES_AV: J7.7, R1.2
PRES: J6.1, R20.2, U2.1
PWM_AR: CON9.1, J6.3
PWM_AV: CON9.2, J6.4
PWM_DROITE: CON9.4, J6.5
PWM_GAUCHE: CON9.3, J6.2
RESET: BP1.1, BP1.2, C5.1, J5.6
RX_BLUETOOTH: CON7.4, J7.6
SCL: J7.1, R6.2, TP13.1 (TP), U5.2 (SCL)
SDA: J7.2, R5.2, TP12.1 (TP), U5.1 (SDA)
SENS_AR: J4.5, R15.2, TP9.1 (TP), U3.1
TONE: J7.8, JP2.1 (A)
TX_BLUETOOTH: CON7.5, J7.5
VIN: CON3.2, J5.1, R3.2
V_AUDIO: CON8.2, Q2.1 (E1)

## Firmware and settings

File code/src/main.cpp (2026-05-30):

//////////////////////////////////////////////////////////////////
//              Déclarations des librairies              /////////
//////////////////////////////////////////////////////////////////
#include <SoftwareSerial.h>     // Librairie pour l'utilisation de la liaison série avec le module Bluetooth
//#include <RemoteXY.h>           // Librairie pour l'utilisation de l'interface graphique du smartphone
#include <Wire.h>               // Librairie pour l'utilisation de l'I2C

/////////////////////////////////////////////////////////////////
//  Déclarations des ALIAS des broches analogiques (pin) /////////
//////////////////////////////////////////////////////////////////
#define CAP_LUM_PIN A0            // Association du mot CAP_LUM_PIN au numéro de broche A0  
#define SENS_AR_PIN A0           
#define DISTANCE_AV_PIN A0        
#define DISTANCE_AR_PIN A0        
#define NIV_BATT A0             
        
/////////////////////////////////////////////////////////////////
//  Déclarations des ALIAS des broches numériques (pin) /////////
/////////////////////////////////////////////////////////////////
const int  PHARES_AR_PIN = 1;   // Association du mot PHARES_AR_PIN au numéro de broche 2 équivalent à "#define PHARES_AR_PIN 2"   
const int  PWM1A_PIN = 1; 
const int  PHARES_AV_PIN = 1; 
const int  CMD_GENE_AUDIO_PIN = 1;
const int  TONE_PIN = 1;  
const int  PRES_PIN = 1;       // Association du mot PRES_PIN au numéro de broche 7 équivalent à "#define PRES_PIN 7"          
const int  LOIN_PIN = 1;
const int  PWM2A_PIN = 1;  
const int  PWM2B_PIN = 1;
const int  PWM1B_PIN = 1;
//const int  RX_PIN = 12;   // Declaration dans la section ci dessous RemoteXY connection settings avec #define
//const int  TX_PIN = 13;   // Declaration dans la section ci dessous RemoteXY connection settings avec #define
const int SDA_PIN = 1;              
const int SCL_PIN = 1;  


//////////////////////////////////////////////
//        RemoteXY include library          //
//////////////////////////////////////////////


/////////////////////////////////////////////
//           END RemoteXY include          //
/////////////////////////////////////////////



///////////////////////////////////////////////////////////////////////////////////////////////////
//                                 LES FONCTIONS                                                 //
///////////////////////////////////////////////////////////////////////////////////////////////////

////////////////////////////////
//  Gestion de la direction   //
////////////////////////////////

/////////////////////////////////
//  Gestion de la propulsion   //
/////////////////////////////////

////////////////////////////////////////////////////////////////////////////////////////////
//  Gestion du bargraph du téléphone de niveau batterie ou de proximité du capteur avant  //
////////////////////////////////////////////////////////////////////////////////////////////

/////////////////////////////////////////
//    Gestion phares                  //
////////////////////////////////////////

////////////////////////////////////////////////////
//    Gestion du buzzer avec Klaxon italien       //
////////////////////////////////////////////////////

//////////////////////////////////////////////////////////////
///// Gestion approche obstacle avant     ////////////////////
//////////////////////////////////////////////////////////////

//////////////////////////////////////////////////////////////////////
/////         Moyennage du capteur avant          ////////////////////
//////////////////////////////////////////////////////////////////////

//////////////////////////////////////////////////////////////////////
/////                 Gestion de la température                 //////
//////////////////////////////////////////////////////////////////////
 void recep_temperature (void)
 {
   static unsigned char temp_Ambiante_entier = 0;
   //static unsigned char temp_Ambiante_frac;
   //float temp;

  // Communication avec le dispositif I2C
   Wire.beginTransmission(0x48);    // Initiation de la communication I2C avec le composant d'adresse 0x48
   Wire.write(0x00);                // Acces au registre de Temperature Ambiante
   Wire.endTransmission(false);     // Réinitialisation de la communication en vue de la réception de données
   Wire.requestFrom(0x48,2);        // Demande de réception des 2 octets de température MSB : signe T6 T5 T4 T3 T2 T1 T0 / LSB : Fraction X X X X X X X X 

   // Lecture des données reçues
   if (2 <= Wire.available())       // Si les 2 octets de données sont reçus
   {
     temp_Ambiante_entier = Wire.read();  // Lecture de l'octet de poids fort MSB : signe T6 T5 T4 T3 T2 T1 T0
     //temp_Ambiante_frac = Wire.read();    // Lecture de l'octet de poids faible LSB : Fraction X X X X X X X X 
   }

  // Interprétation des données et envoie sur l'interface graphique
  //.................
 }


//////////////////////////////////////////////////////
//              Initialisation                      //
//////////////////////////////////////////////////////
void setup()
{
  //////////////////////////////////////////////////////////////////
  // Initialisation des broches numériques en entrée ou en sortie //
  //////////////////////////////////////////////////////////////////
  pinMode(PHARES_AR_PIN, INPUT);

  ///////////////////////////////////////////////////////////////////
  // Initialisation des 6 broches analogiques en entrée ou en sortie //
  ///////////////////////////////////////////////////////////////////
  pinMode(CAP_LUM_PIN, INPUT);
 
  /////////////////////////////////////////////////////////////////////
  // Initialisation communication liaison série                    //
  ///////////////////////////////////////////////////////////////////

  /////////////////////////////////////////////////////////////////////
  // Initialisation communication avec l'interface graphique        //
  ////////////////////////////////////////////////////////////////////

  /////////////////////////////////////////////////////////////////////
  // Initialisation communication I2C                                //
  /////////////////////////////////////////////////////////////////////
  Wire.setSCL(SCL_PIN);
  Wire.setSDA(SDA_PIN);
  Wire.begin();
}



///////////////////////////////////////////////////////
//                 Boucle infinie                   ///
///////////////////////////////////////////////////////
void loop()
{
  /////////////////////////////////////////////////////////////////////
  //  communication avec l'interface graphique                       //
  /////////////////////////////////////////////////////////////////////
  
  
  
  // déclaration des variables
  bool sens_av;   // Le véhicule se rapproche de l'obstacle en marche avant  => sens_av=true sinon sens_av=false
  bool sens_ar;   // Le véhicule se rapproche de l'obstacle en marche arriere  => sens_ar=false sinon sens_ar=true
  int capt_av;    // Variable contenant la moyenne de valeur de la conversion du capteur avant 
  int niv_batt;   // Variable contenant une information sur la tension batterie (8.7V batterie pleine -> 3.3V sur convertisseur; 6,5V batterie vide -> 2.5V sur convertisseur)
  bool pres;      // Variable indiquant la position pres du véhicule avec un obstacle arriere
  bool loin;      // Variable indiquant la position loin du véhicule avec un obstacle arriere
  bool freinage;  // Variable indiquant un freinage (freinage = 1)
  



//

  ///////////////////////////////////////
  //  Informations de l'environnement  //
  ///////////////////////////////////////
  pres = digitalRead (PRES_PIN);              // sommes nous dans la zone près arrière
  loin = digitalRead (LOIN_PIN);              // sommes nous dans la zone loin arrière
  sens_ar = digitalRead (SENS_AR_PIN);        // sens_ar=0 => la voiture et l'obstacle arrière se rapprochent
                                              // La valeur numérique de capt_av correspond à la distance entre la voiture et l'obstacle
                                              // sens_av=1 => la voiture et l'obstacle avant se rapprochent
                                              // niv_batt tension image de la tension batterie


  ///////////////////////////////
  //  Pilotage de la voiture   //
  ///////////////////////////////
  
}

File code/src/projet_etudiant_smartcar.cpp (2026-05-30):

////////////////////////////////////////////////////////
//              Inclusion des librairies              //
////////////////////////////////////////////////////////
#include <Wire.h> // Librairie pour l'utilisation de l'I2C
#define SoftwareSerial_h

///////////////////////////////////////////////////////////
//  Déclarations des ALIAS des broches analogiques (pin) //
///////////////////////////////////////////////////////////
#define CAP_LUM_PIN A0  // le terme CAP_LUM_PIN sera remplacé par le compilateur* par le terme A0 (*par le préprocesseur)
#define SENS_AR_PIN PA1 // changé de A1 à PA1 par Regis Nohe
#define DISTANCE_AV_PIN A2
#define DISTANCE_AR_PIN A3
#define NIV_BATT_PIN A4

///////////////////////////////////////////////
//  Déclarations des ALIAS des broches (pin) //
///////////////////////////////////////////////
const uint32_t PHARES_AR_PIN = D2;
const uint32_t PHARES_AV_PIN = D11;

const uint32_t CMD_GENE_AUDIO_PIN = D9;
const uint32_t TONE_PIN = D10;
const uint32_t PRES_PIN = D7;
const uint32_t LOIN_PIN = D8;

const uint32_t PWM_AVANT_PIN = D4;
const uint32_t PWM_ARRIERE_PIN = D5;
const uint32_t PWM_DROITE_PIN = D3;
const uint32_t PWM_GAUCHE_PIN = D6;

const uint16_t RX_PIN = D12; // mettre à jour les #define des codes générés par RemoteXY
const uint16_t TX_PIN = D13; // mettre à jour les #define des codes générés par RemoteXY

const uint32_t SDA_PIN = D14;
const uint32_t SCL_PIN = D15;

// Déclaration des canaux utilisés pour les PWM  //
const uint32_t CANAL_DROITE = 2;
const uint32_t CANAL_GAUCHE = 3;
const uint32_t CANAL_PHARE = 3;   // Le canal pour phares arrière
const uint32_t CANAL_AVANT = 3;   // canal 3 pour la propulsion avant
const uint32_t CANAL_ARRIERE = 2; // canal 2 pour la propulsion arrière

// Déclaration des timers            //
HardwareTimer timerDirection(TIM2);
HardwareTimer timerPropulsion(TIM3);
HardwareTimer timerPhares(TIM4);

//////////////////////////////////////////////
//        RemoteXY include library          //
//////////////////////////////////////////////

// you can enable debug logging to Serial at 115200
// #define REMOTEXY__DEBUGLOG

// RemoteXY select connection mode and include library
#define REMOTEXY_MODE__SOFTSERIAL

#include <SoftwareSerial.h>

// RemoteXY connection settings
#define REMOTEXY_SERIAL_RX 12
#define REMOTEXY_SERIAL_TX 13
#define REMOTEXY_SERIAL_SPEED 9600

#include <RemoteXY.h>

// RemoteXY GUI configuration
#pragma pack(push, 1)
uint8_t const PROGMEM RemoteXY_CONF_PROGMEM[] = // 106 bytes V19
    {255, 3, 0, 15, 0, 99, 0, 19, 0, 0, 0, 0, 31, 2, 106, 200, 200, 84, 1, 1,
     5, 0, 73, 90, 10, 7, 76, 174, 5, 14, 32, 4, 128, 19, 135, 26, 0, 0, 0, 0,
     0, 0, 200, 66, 0, 0, 0, 0, 67, 81, 155, 21, 24, 8, 6, 40, 10, 70, 2, 26,
     11, 5, 251, 17, 143, 143, 110, 17, 58, 58, 32, 2, 26, 31, 1, 240, 60, 57, 57, 17,
     39, 24, 24, 0, 2, 31, 0, 129, 12, 78, 71, 29, 69, 5, 55, 12, 64, 17, 83, 77,
     65, 84, 67, 65, 82, 0};

// this structure defines all the variables and events of your control interface
struct
{

  // input variables
  int8_t joystick_01_x; // from -100 to 100
  int8_t joystick_01_y; // from -100 to 100
  uint8_t klaxon;       // =1 if button pressed, else =0, from 0 to 1

  // output variables
  float Bargraph;      // from 0 to 100
  char zone_texte[11]; // string UTF8 end zero

  // other variable
  uint8_t connect_flag; // =1 if wire connected, else =0

} RemoteXY;
#pragma pack(pop)

/////////////////////////////////////////////
//           END RemoteXY include          //
/////////////////////////////////////////////

////////////////////////////////////////////////////////////////////////////////////////////
//                                 DEFINITIONS DE FONCTIONS                               //
////////////////////////////////////////////////////////////////////////////////////////////
int PWM_DROITE; // commande la direction à droite
int PWM_GAUCHE; // commande la direction à gauche
int joystickX;  // La la valeur que renvoie joystick sur l'axe X (-100 ≤ valeur de l'axe X ≤ 100)

int connexion_bluetooth;
int PWM_AVANT;
int PWM_ARRIERE;

////////////////////////////////
//  Gestion de la direction   //
////////////////////////////////
void pwm_direction()
{
  int8_t joystick_x = RemoteXY.joystick_01_x;  // joystick (-100 à +100)

  if (RemoteXY.connect_flag == 1) // Si telephone connecte
  {
    if (joystick_x > 10)          // Tourner a droite
    {
      timerDirection.setCaptureCompare(CANAL_DROITE, joystick_x);  // moteur droite actif
      timerDirection.setCaptureCompare(CANAL_GAUCHE, 0);           // moteur gauche a l'arrêt
    }
    else if (joystick_x < -10)    // Tourner a gauche
    {
      timerDirection.setCaptureCompare(CANAL_DROITE, 0);                  // moteur droite à l'arrêt
      timerDirection.setCaptureCompare(CANAL_GAUCHE, (-1) * joystick_x);  // moteur gauche actif
    }
    else // zone morte (joystick centré)
    {
      timerDirection.setCaptureCompare(CANAL_DROITE, 0);  // moteur droite a l'arrêt
      timerDirection.setCaptureCompare(CANAL_GAUCHE, 0);  // moteur gauche à l'arrêt
    }
  }

  Serial.println(joystick_x);  // debuuuug
}

/////////////////////////////////
//  Gestion de la propulsion   //
/////////////////////////////////
bool pwm_propulsion(bool p, bool l, bool s_ar)
{
  bool freiner = 0;

  if (RemoteXY.connect_flag == 1)
  {
    if (RemoteXY.joystick_01_y > 10)
    {
      timerPropulsion.setCaptureCompare(CANAL_AVANT, RemoteXY.joystick_01_y);
      timerPropulsion.setCaptureCompare(CANAL_ARRIERE, 0);
    }

    else if (RemoteXY.joystick_01_y < -10)
    {
      if (l == 1)
      {
        timerPropulsion.setCaptureCompare(CANAL_AVANT, 0);
        timerPropulsion.setCaptureCompare(CANAL_ARRIERE, (RemoteXY.joystick_01_y * (-1)));
      }
      else if (p == 0)
      {
        timerPropulsion.setCaptureCompare(CANAL_AVANT, 0);
        timerPropulsion.setCaptureCompare(CANAL_ARRIERE, (RemoteXY.joystick_01_y * (-1)) / 2);
      }
      else
      {
        if (s_ar == false)
        {
          timerPropulsion.setCaptureCompare(CANAL_AVANT, 100);
          timerPropulsion.setCaptureCompare(CANAL_ARRIERE, 0);
          freiner = true;
        }
        else
        {
          timerPropulsion.setCaptureCompare(CANAL_AVANT, 0);
          timerPropulsion.setCaptureCompare(CANAL_ARRIERE, 0);
        }
      }
    }
    else
    { // si la joystick est au milieu
      if (p == 1)
      {
        if (s_ar == false)
        {
          timerPropulsion.setCaptureCompare(CANAL_AVANT, 100);
          timerPropulsion.setCaptureCompare(CANAL_ARRIERE, 0);
          freiner = true;
        }
        else
        {
          timerPropulsion.setCaptureCompare(CANAL_AVANT, 0);
          timerPropulsion.setCaptureCompare(CANAL_ARRIERE, 0);
        }
      }
      else
      {
        timerPropulsion.setCaptureCompare(CANAL_AVANT, 0);
        timerPropulsion.setCaptureCompare(CANAL_ARRIERE, 0);
      }
    }
  }
  return freiner;
}
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

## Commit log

2026-05-30 Ajout des dossiers code, hardware et docs
    [SmartCar_Etudiant-B_Cu.gbr, SmartCar_Etudiant-B_Mask.gbr, SmartCar_Etudiant-B_Paste.gbr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]
2026-05-31 Rename Réalisation de la carte shield DELANNEEDERNIERE.pdf to Réalisation de la carte shield.pdf
2026-05-31 Rename Présentation de la SAE1_S2.pdf to Présentation_de_la_SAE1_S2.pdf
2026-05-31 Rename Présentation_de_la_SAE1_S2.pdf to Présentation de la SAE1 S2.pdf
